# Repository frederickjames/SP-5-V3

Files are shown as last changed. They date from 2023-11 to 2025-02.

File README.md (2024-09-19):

# SP-5 V3

This project documents the work I've done in an attempt to make the Two Trees SP-5 V3 printer produce quality prints faster than the ol' reliable Ender 3 Pro. I hope some of this can help the community that, like me, purchases ~~cheap~~ less expensive stuff and enjoys the tinkering process.

### Summary of Project

- [Orange Pi Zero 3 for Klipper](/Orange%20Pi%20Zero%203/)
- [Klipper Config](/Klipper%20Config/)
- [Other modifications](/Other%20Modifications/)
 - [Hotend](/Other%20Modifications#v6-cheap-clone-hotend)
 - [ABL (3D Touch knockoff)](/Other%20Modifications#automatic-bed-leveling-and-probing)
 - [Silicone bed "springs"](/Other%20Modifications#springs)
 - [Z-Axis Changes](/Other%20Modifications#z-axis)

### Fixing Motion System

The linear rails were not smooth. On my priner the y-axis was particularly bad.  I finally got over my fear of losing all my bearings and broke down the linear rails to clean and lubricate.  I used Liquid Wrench to clean the rails and underside of the carriage then lubed with a little extra Super Lube applied by syringe.

To remove the carriage from the rails, invert the rail so the carriage is on the bottom the slowly slide it off the end of the rail trying to keep it as level as possible.  Once removed you'll see a row of ball bearings lightly held in place by a thin, flexible wire.  Take extra care when cleaning the underside of the carriage as any slight bump can cause the ball bearings to go flying (I wouldn't know anything about that).

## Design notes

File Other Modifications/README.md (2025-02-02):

# Other Modifications

Modifications were needed to tune this thing and make it print way nicer. Outside of updating to klipper and running it off of an Orange Pi, here are the modifications:

- All metal hotend (It's 2023, get the PTFE out of the melt zone)
- [Even better hotend solution](#v6-cheap-clone-hotend)
- [ABL (3D Touch knockoff)](#automatic-bed-leveling-and-probing)
- [Silicone bed "springs"](#springs)
- [Rigid shaft couplings between the stepper and the Z lead screws](#z-axis)
- [Oldham couplings for the Z lead screws](#z-axis)
- [Thrust Bearings to support the Z lead screws](#z-axis)

---

## All Metal Hotend

#### I have a [new solution](#v6-cheap-clone-hotend)

~~I found  some parts on Amazon that had close enough dimensions. I think they are a long way from good, but no worse than the stock setup.  I'll look around for hotend upgrades and update when I find something better.~~

- ~~[Some random Titanium Alloy Therman Heat Break](https://www.amazon.com/dp/B07JD2S4GK)~~
- ~~[Some cheap nozzles that are long enough to meet the heatbreak in the heater block](https://www.amazon.com/dp/B0C283TNWK)~~

~~You may also want to print [new 4010 Ducts](4010%20Duct%20Replacement.3mf). I only made these because I broke one of the existing ducts.  If you want to use it, you'll need to print it as is and a mirror for the left side.~~

---

## V6 (cheap clone) Hotend

I changed the hotend. The modifications I previously did where lackluster. I got tired of repairing and when it fell apart this time I just decided to replace.  I came across an old [YouTube from ModBot](https://www.youtube.com/watch?v=cXx1_OsDcIc) where he put an E3Dv6 on an older Two Trees coreXY.  Inspired by the mount he found, [I designed my own](V6%20Mount) and purchased a [cheap V6 clone from Amazon](https://www.amazon.com/dp/B0BR7Z63H8).

*UPDATE 2025-01-30: *I noticed that the bare plastic version where the M3 cut the threads was a little wobbly. It still printed, but I needed an excuse to make something. So I added a version with threaded inserts for the main body that holds the heatsink. You'll need 4 M3x6x5 threaded inserts.

---

## Automatic Bed Leveling and Probing

The knockoff kind of BL Touch that the Klipper documentation warns you about. It doesn't respond to the self test or some of the other diagnostic stuff, but it works.  You can see the setup in [the config file](../Klipper%20Config/printer.cfg).

Print [this crappy mount if you want](Touch%20Mount.3mf). ~~I may redesign later, but probably only if this one breaks or I take off the useless metal shroud it's attached to (more likely).~~

Offsets for crappy mount:  
x_offset: -33  
y_offset: 25  
z_offset: 3.00  

Or, when that one breaks becasue it's crap and you want to remove the useless metal shroud so you can see what's going on, you can [print this mount](Touch%20Mount%20-%20Back.3mf). It screws to the back of the print head where the rear shroud was attached. You will need longer M3 screws (I used M3x10mm, but 8mm would work too).

Offsets for less crappy mount:\
x_offset: 0\
y_offset: 25\
z_offset: 3.1

Both mounts are likely compatible with other Touch probes like the BL and Creality, but I have not tested.

- [3D Touch](https://www.amazon.com/dp/B09M9V8Y4Y "trust me, bro.")

---

## Springs

Probably not necessary, but I like them and they are cheap. I did have to make [some little spacers](SiliconeBedMountSpacers.3mf "put them on the bottom") to go under the Silicone springs becasue they were not tall enough.

- [3D Printer Heat Bed Leveling Parts](https://www.amazon.com/dp/B093Y89KS9)

---

## Z Axis

I was having a lot of trouble with z wobble and high pitch squeaking noise as the z axis moved so I looked at a bunch of videos and other stuff. Below is a list of what I did to change address the issue.
Starting from the bottom and working my way up, I put thrust bearings under the coupler to get the weaight of the Z assembly off the motors. They are held in place with a [little print](NEMA17_Thrust_Bearing_Holder.3mf) that fits over the heads of the motor mount screws.
Next up was replacing the flexible coupler. Using a flexible coupler to account for misaligned and wavy lead screws is low effort and does more to just allow the Z-axis to move than it does to correct the issue. I replaced with rigid shaft couplers. BUT only do this if you are addressing the lead screw binding with a different method (like oldham or wobblex).
Finally on the lead screw I added Oldham Couplers. Almost went with the WobbleX, but this thing called an Oldham showed up in search results and is like half the price so I gave it a try. I found [an adapter](https://www.printables.com/model/376711-sp-5-oldham-coupling-adapter) by [UNIT_normal](https://www.printables.com/@UNIT_normal_528315) on printables.

- [Thrust Bearings](https://www.amazon.com/gp/product/B07QLTXJDH "Maybe unneceary, but they are cheap.")
- [Rigid Shaft Coupling](https://www.amazon.com/dp/B08ZJ854Z6 "They don't do yoga")
- [Oldham](https://www.amazon.com/dp/B0BQMWC1VG "Named for leftovers past their prime.")

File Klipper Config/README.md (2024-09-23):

# Klipper Settings

### Printer Config
The [printer.cfg](printer.cfg) is based on the stock SP-5 V3 motherboard, Makerbase Robin Nano v3.1

### Macros
If you want to use the [macros](SP-5_V3_macro.cfg) for start/end, replace the existing start and end G-code with the following. The START_PRINT macro assumes you have a mesh named default. (Works in Cura, ymmv.)
#### Cura:
Start G-code:
```
START_PRINT BED_TEMP={material_bed_temperature_layer_0} EXTRUDER_TEMP={material_print_temperature_layer_0}
```
End G-code:
```
END_PRINT
```
#### Orca and similar:
Machine start G-code:
```
START_PRINT EXTRUDER_TEMP=[nozzle_temperature_initial_layer] BED_TEMP=[bed_temperature_initial_layer_single]
```
Machine end G-code:
```
END_PRINT
```

I moved my heatsync fan to J6 so it can be turned on/off as needed instead of always running. The printer.cfg file is set up for this, but it's optional to move the fan since J5 is always on. Do what you want, I'm not your dad. A word of warning, if you move the wrong plug then the case fans won't run all the time like they are currently set to so be sure you know which plug is case fans and which is hot end cooler.

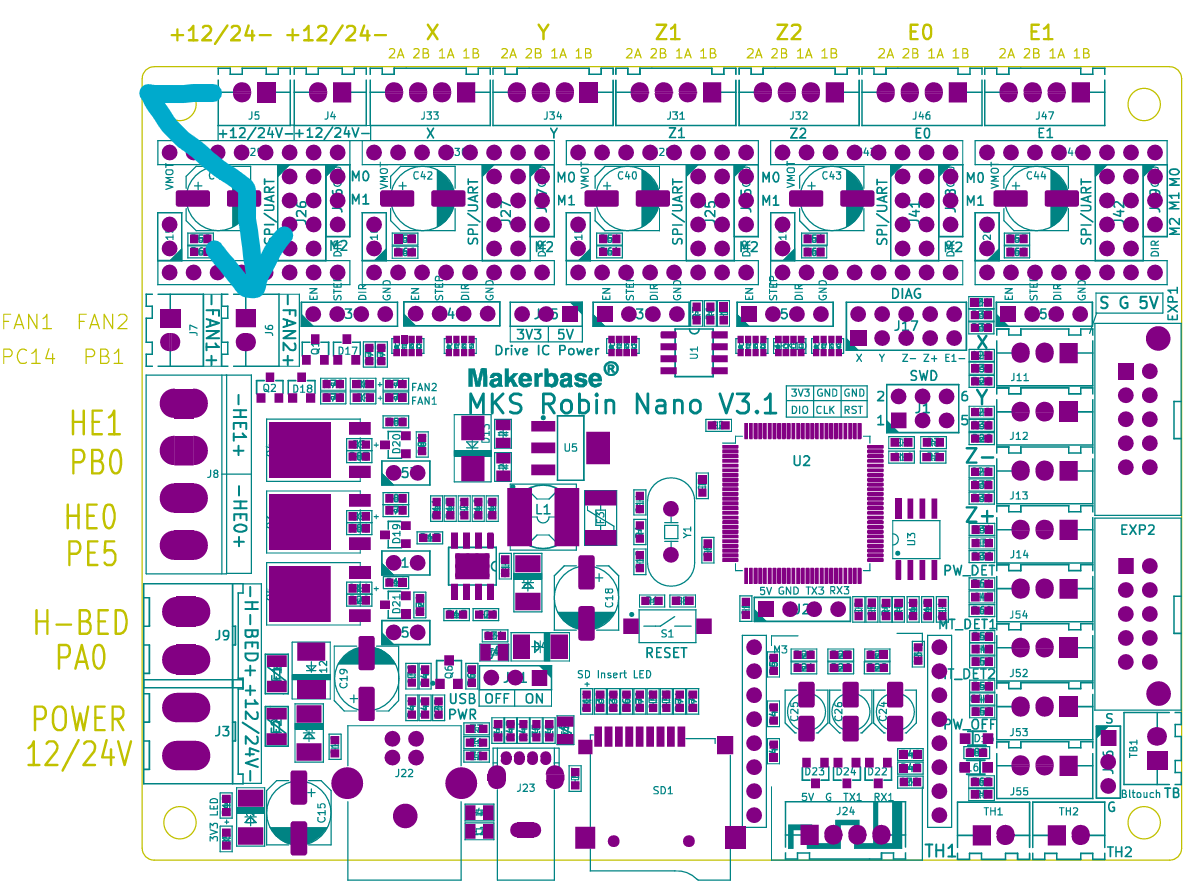
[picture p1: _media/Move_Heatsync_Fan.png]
J5 to J6 Optional Fan Move


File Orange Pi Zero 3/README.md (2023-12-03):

# Orange Pi Zero 3

This directory contains information on utilizing the Orange PI Zero 3 1.5G to run Klipper. Including the files to print a case for the board will replace the printers electronics cover. The case allows for access to the Orange PI's I/O through an enclsure built around the SP-5 V3 frame. You could probably just put whatever flavor of Pi you want under the deck with the rest of the electronics. Do what you want, I'm not youre dad.

I am using a UART connection between Orange Pi Zero 3 and the Robin Nano v3.1. UART setup on the Pi can be found [here on the Orange Pi Wiki](http://www.orangepi.org/orangepiwiki/index.php/Orange_Pi_Zero_3#26pin_UART_test). Pin connections depicted below, be sure to conenct Tx to Rx and Rx to Tx. Or just use USB if you want; I'm not your dad. But USB won't work with the case.

|Orange Pi Pin |Function | Function | Rodin Nano Pin|
|:---|:---|---:|---:|
|6|GND|GND|J2 Header - 2|
|8|TX|RX|J2 Header - 4|
|10|RX|TX|J2 Header - 3|

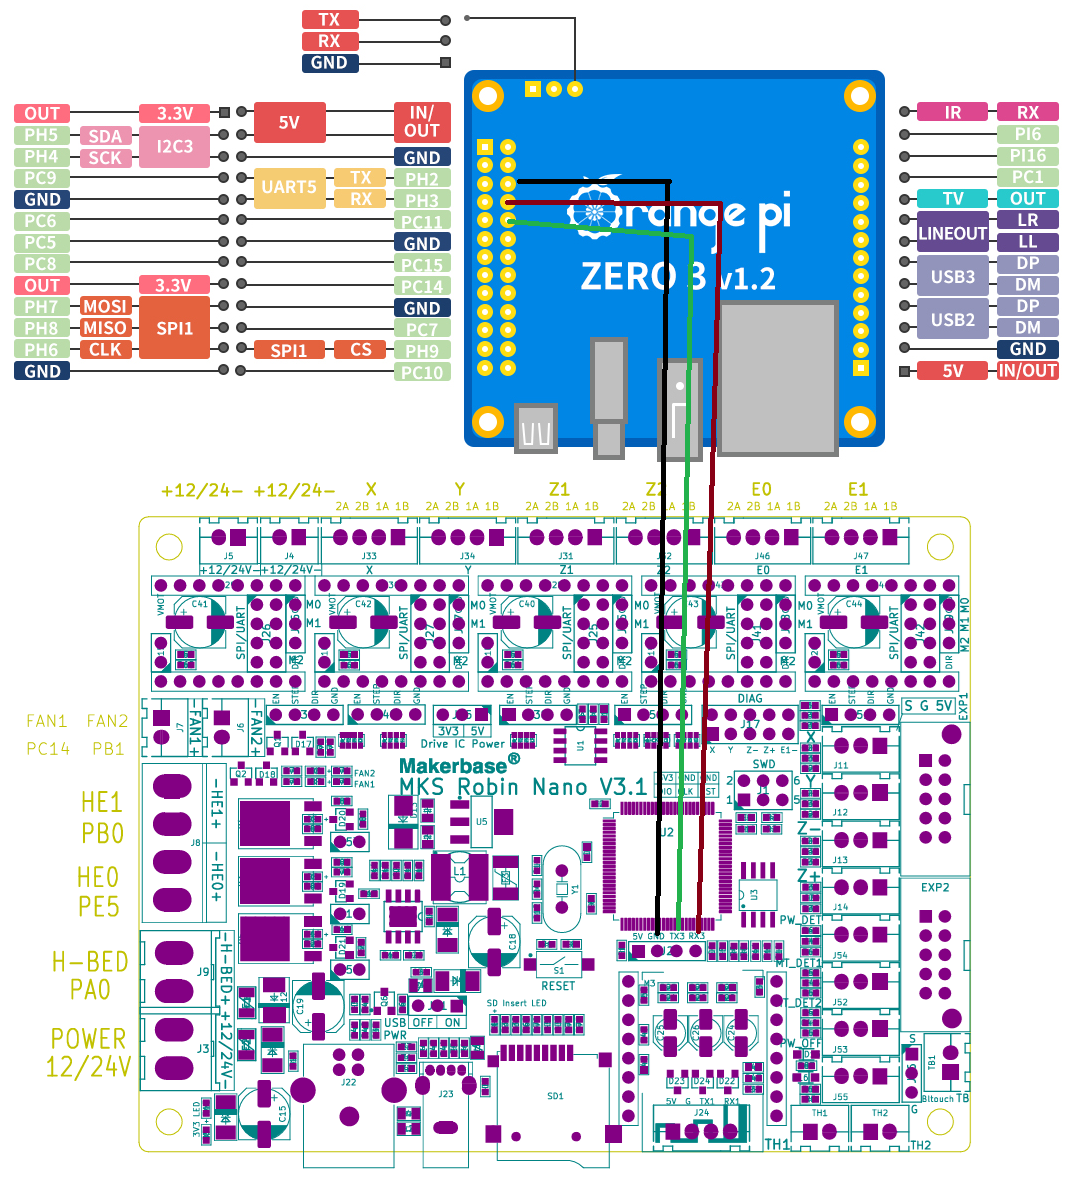
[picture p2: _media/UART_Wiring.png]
Cross the streams becasue you're not a ghost buster.


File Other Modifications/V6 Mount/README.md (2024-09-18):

# V6 (style) Hotend Bracket

I came across an old [YouTube from ModBot](https://www.youtube.com/watch?v=cXx1_OsDcIc) where he put an E3Dv6 on an older Two Trees coreXY.  Inspired by the mount he found, I designed one for the SP5-V3 and purchased a [cheap V6 clone from Amazon](https://www.amazon.com/dp/B0BR7Z63H8).  Inspired by the mount he found, [I designed my own](V6%20Hotend%20Mount.step).

It is basically a replacement for the bracke that the stock heatsink is attached too and reuses some stock parts.

There are 4 parts to print wth the Touch Mount being optional (if you don't use a touch probe, you don't need the mount). [Front](Front.3mf) and [Back](Back.3mf) are the pieces that hold the heatsink. They are held together by the fan mounting brackets that come with the printer and further supported when installed in the carriage. The [3010 mount](3010 mount.3mf) is screwed into the bottom of the Front. It reuses the 3010 fan from the heatsink that came with the printer. You'll need a new piece of PTFE tube since it's a bit further than before.

### To assemble:

1. Remove the stock hotend, heatsink fan, and 4010 blower fan mounts from the stock carriage and the extruder.
2. Attach the [3010 mount](3010%20mount.3mf) using 2 M3x10 screws from the top.
3. Clamp the [Front](Front.3mf) and [Back](Back.3mf) around the neck of the Heatsink and hold in place with the stock part cooler fan mounts using M3x6 (or M3x8). Right and left side are different - the nozzle should be lined up roughly with the middle of the fan mount.
4. Insert the new PTFE tube
    1. Cut a new piece of PTFE tubing. My final length is about 60.5 mm, but I would recommend you cut it a bit longer and trim it later.
    2. Place it into the hot end making sure it is firmly seated
    3. Slip the [PTFE Brace](PTFE%20Brace.3mf) over the tube with the notch at the top.  It's purpose is to keep the tube straight (I had some blowouts trying to push the filament too hard).
5. The assembly so far will attach to the carriage in the same location as the heatsink brack was removed reusing the M3x8 bolts, but it's a bit tricky.
    1. Slide the assembly up from the bottom passing the PTFE through the hole in the trolly. Make sure to align the notch at the top is facing the linear rail (the notch is allowance for the carriage)
    1. The 2 posts in the back of the assembly will go on the outside of the carriage. To insert the screw, I passed my Allen key through the front mounting holes then passed the M3 screw in from the side with tweezers so I could screw from inside.
    2. After the back is screwed in, you can insert the M3's to fasten the front.
6. Attach the stock part cooler fans and routh the cables as you see fit.
7. Optional: Add "heat shield" above nozzle.
    1. Measure the dimensions between the fan mounts and from front to back and determine (mine was 34mm wide x 37mm deep)
    2. Cut an aluminum can to these dimention plus a little bit wider.
    3. Use the extra width to bent the edges up in otder to give the shield a little more stiffness.
    4. Measure the depth of the heatsink and cut the aluminum to allow the shield to slide between the fins and around the core of the heatsink.
    5. Slide into place between the lowest 2 fins. It will keep the fan directed on the heatsink and away from the nozzle.
8. Install the heatsink fan. If you completed optional step 7, then the bottom of the fan should be in contact with the surface of the heat shield.
8. Replace the extruder assebmbly, trimming the PTFE tube to be the exact length needed.
9. Optional: Install touch probe.
    1. Fasten the probe to the mounting bracket from the bottom using M3x6 screws (or however yo want to fasten it).
    2. Loosly fasten the mount to the back of Back using M3x10 screws through the elongated holes and into the bottom set of holes on the main body.
    3. Adjust the mount to the desired height and tickets the screws to hold it in place.
10. PID tune the new hotend.
```
 PID_CALIBRATE HEATER=extruder TARGET=210
```

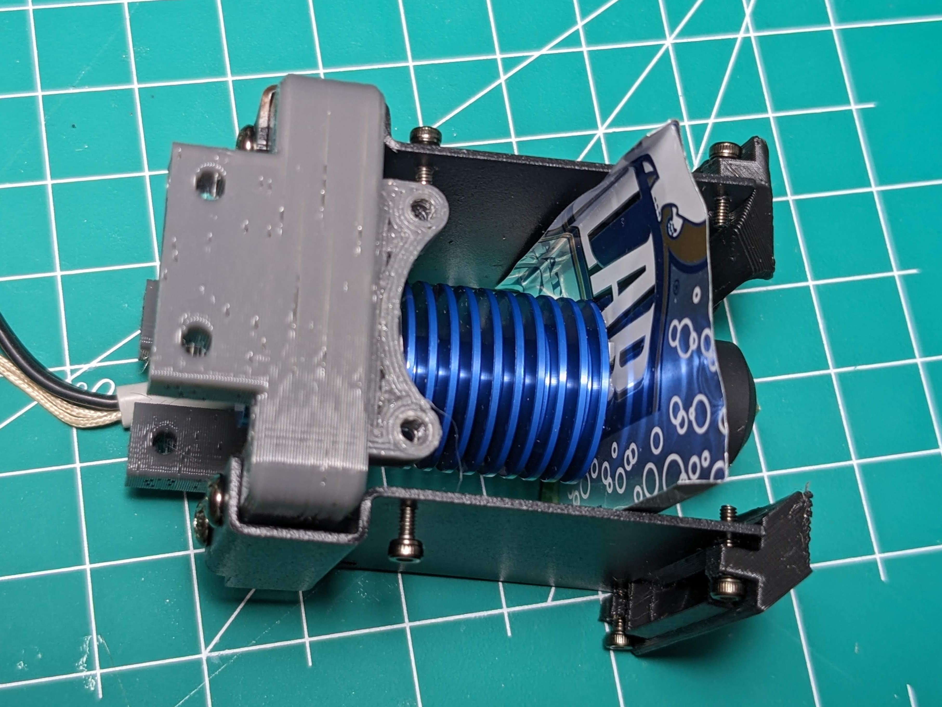
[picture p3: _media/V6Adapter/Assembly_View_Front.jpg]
Assembly front Assembly in progress, front view.

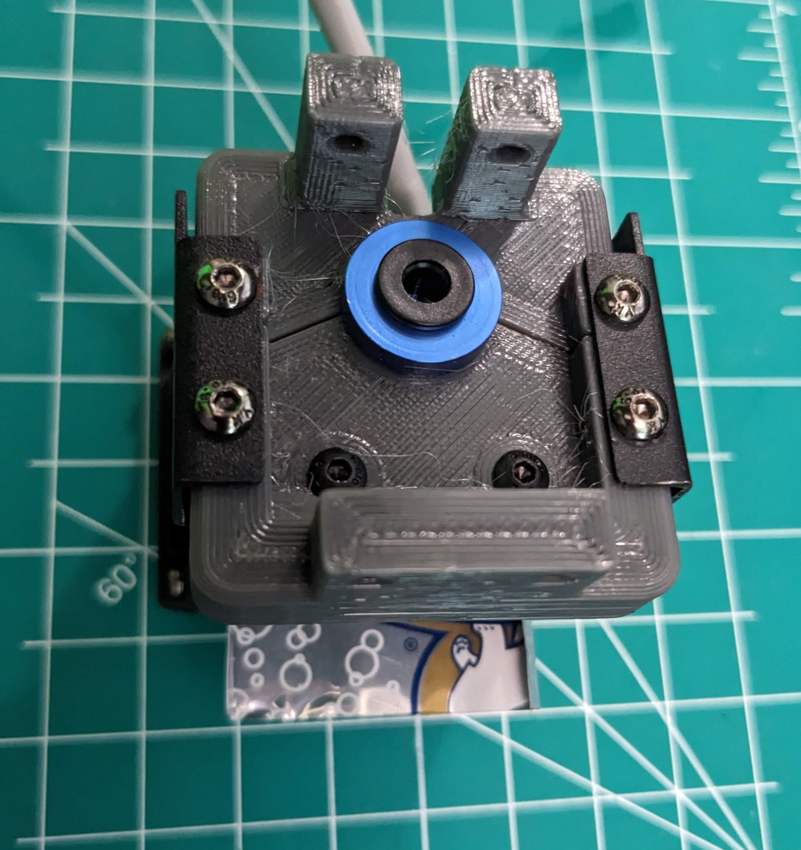
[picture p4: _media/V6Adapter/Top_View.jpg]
Assembly top Assembly in progress, top view.

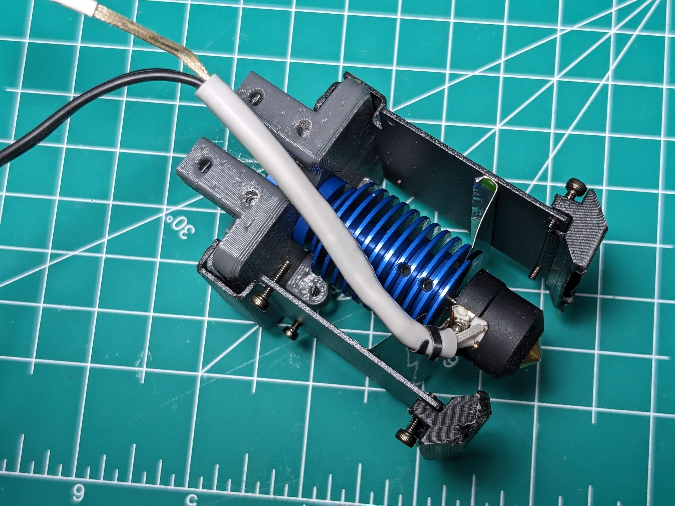
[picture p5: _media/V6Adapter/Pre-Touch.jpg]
Assembly back Assembly in progress, back view.

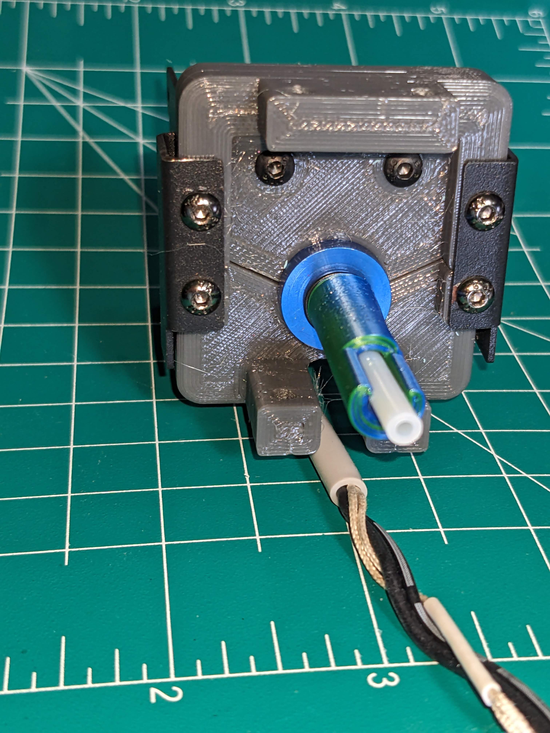
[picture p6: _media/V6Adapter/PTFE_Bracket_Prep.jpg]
PTFE Brace fitted It's pretty

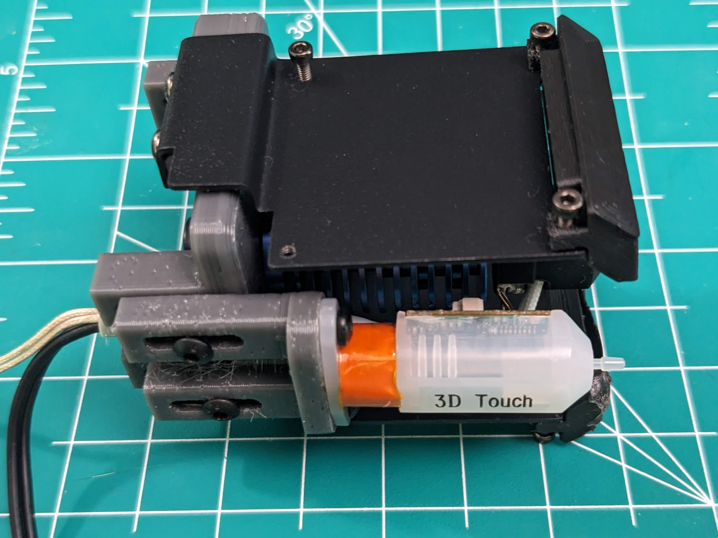
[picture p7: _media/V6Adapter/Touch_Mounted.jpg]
Assembly back quarter with touch mounted Assembly in progress, back quarter view.

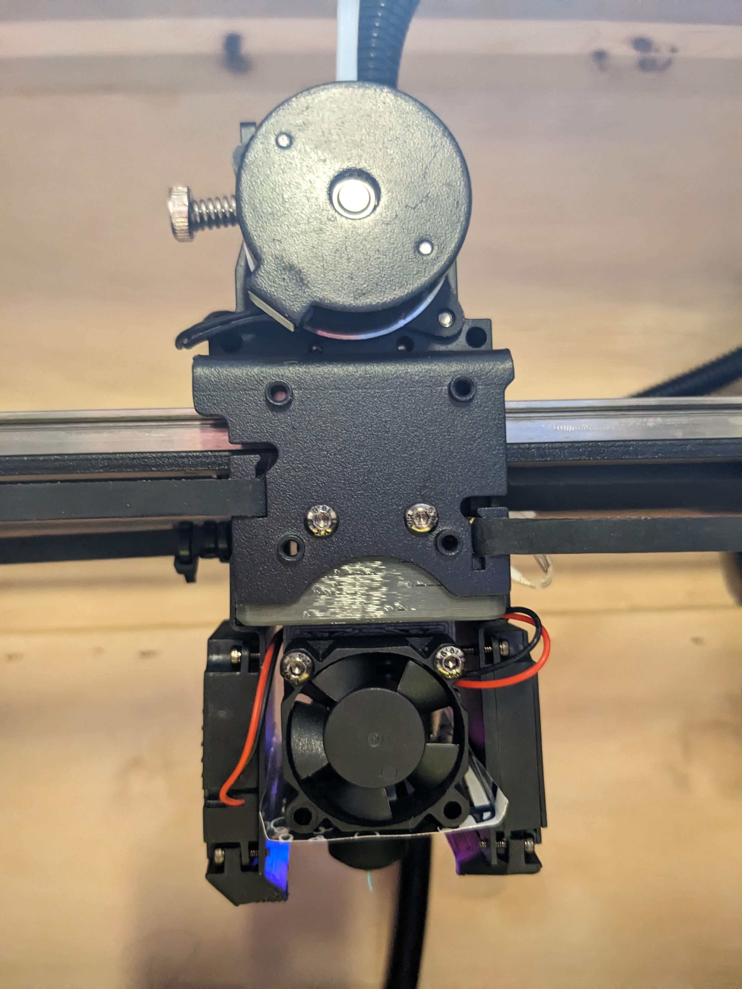
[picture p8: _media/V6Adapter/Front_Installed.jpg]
Front view.

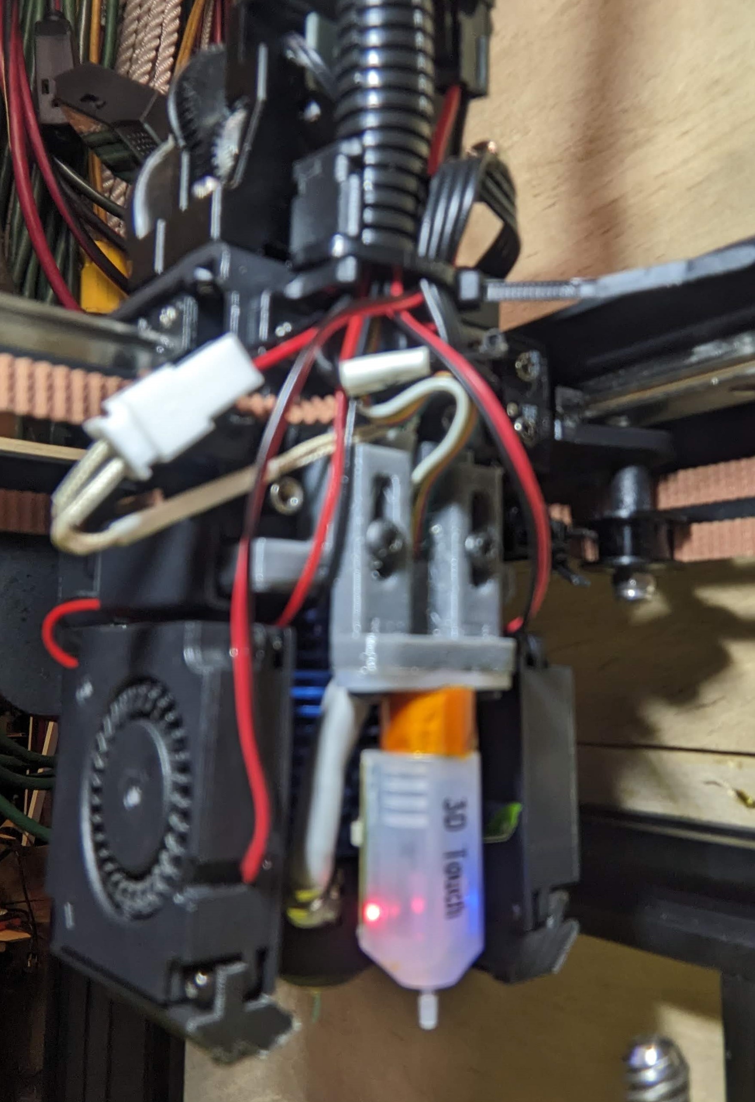
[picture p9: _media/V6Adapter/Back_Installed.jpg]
Out of focus back view.
.
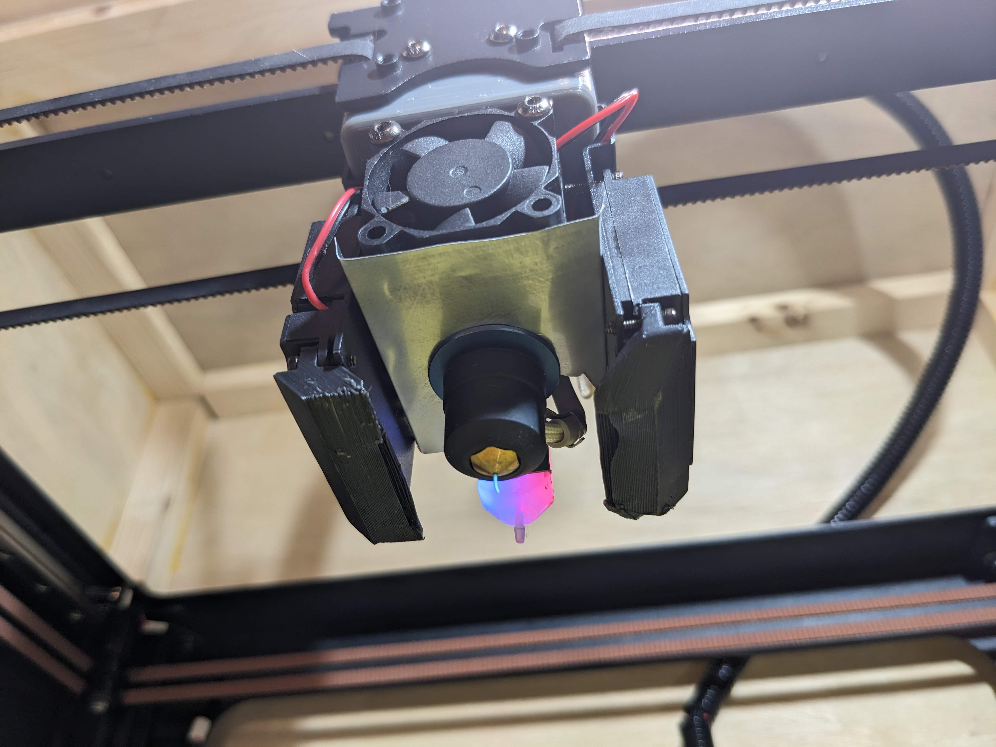
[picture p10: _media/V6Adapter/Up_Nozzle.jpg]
"Heat Shield" viewed from below Heat shield installed - bottom view.

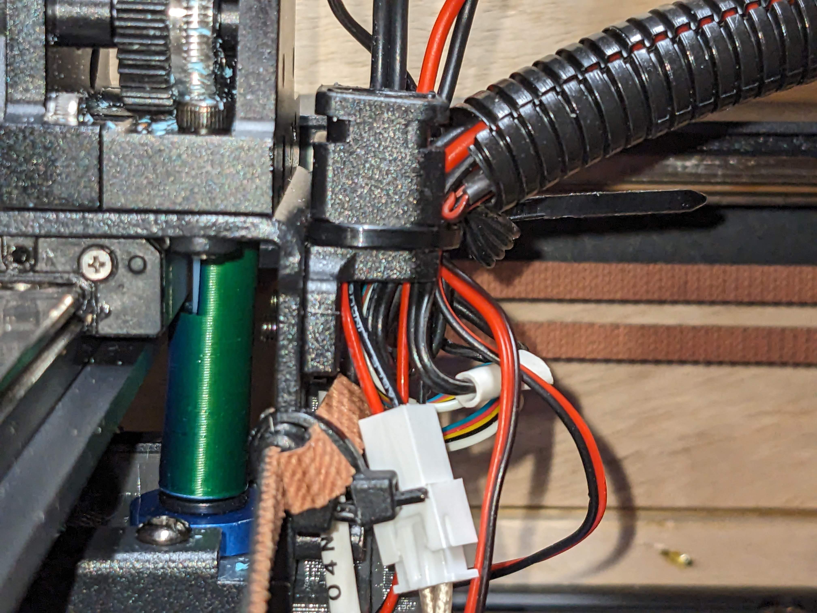
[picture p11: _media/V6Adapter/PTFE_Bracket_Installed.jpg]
PTFE Brce installed It's tight, but it fits.

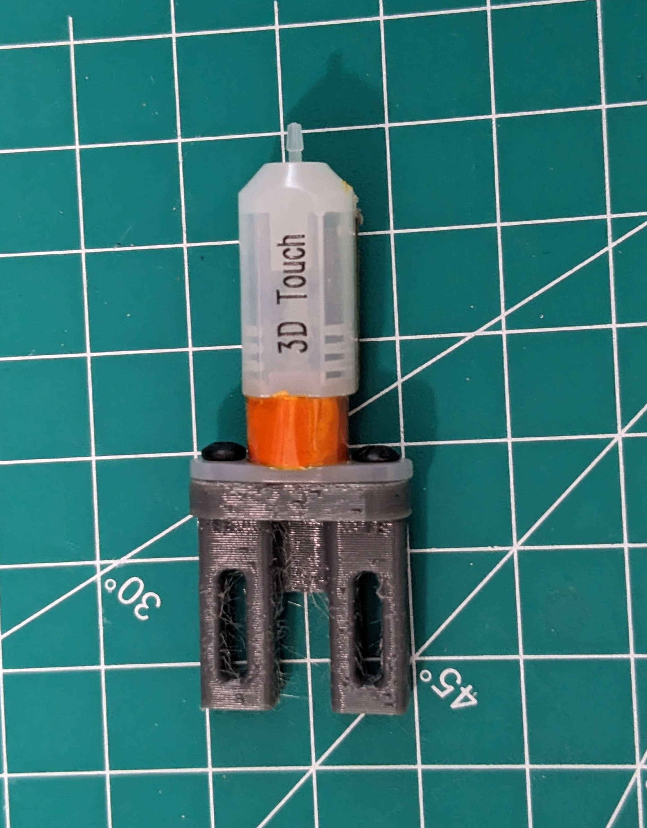
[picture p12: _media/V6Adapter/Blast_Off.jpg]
BLAST OFF!


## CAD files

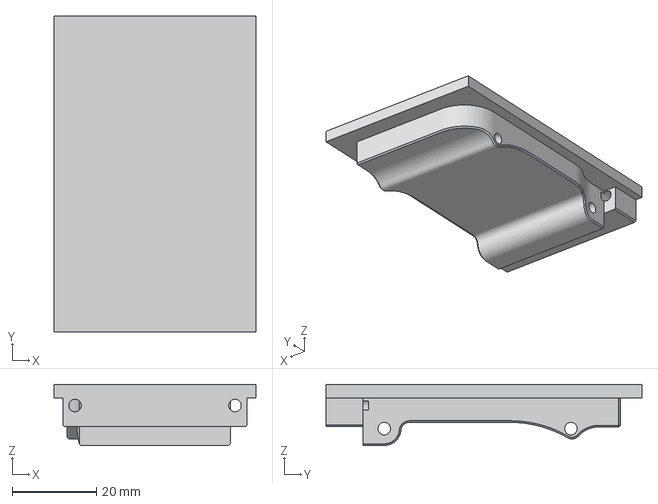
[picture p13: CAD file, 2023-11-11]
Orange Pi Zero 3/Top.3mf
48.0 x 75.0 x 14.5 mm

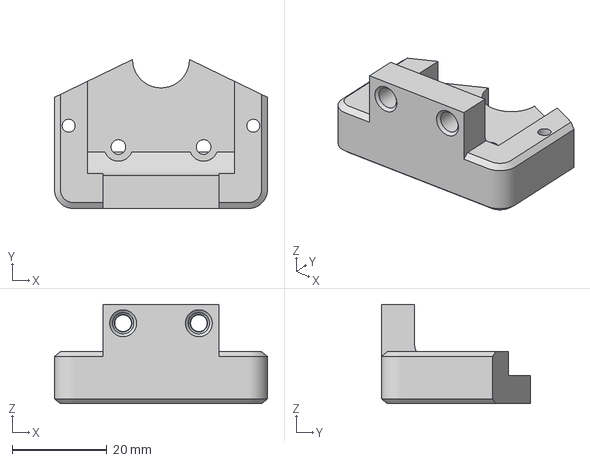
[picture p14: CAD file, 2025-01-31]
Other Modifications/Front.3mf
45.0 x 31.5 x 21.0 mm

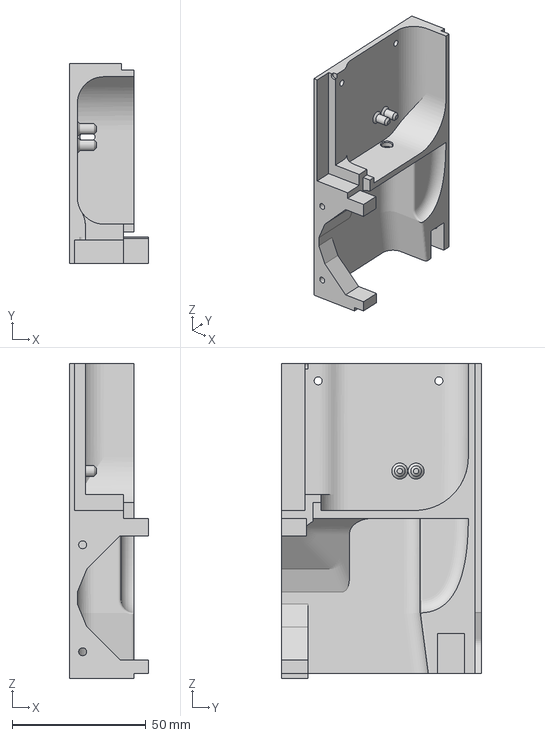
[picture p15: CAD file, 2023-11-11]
Orange Pi Zero 3/Side.3mf
29.7 x 75.0 x 117.9 mm

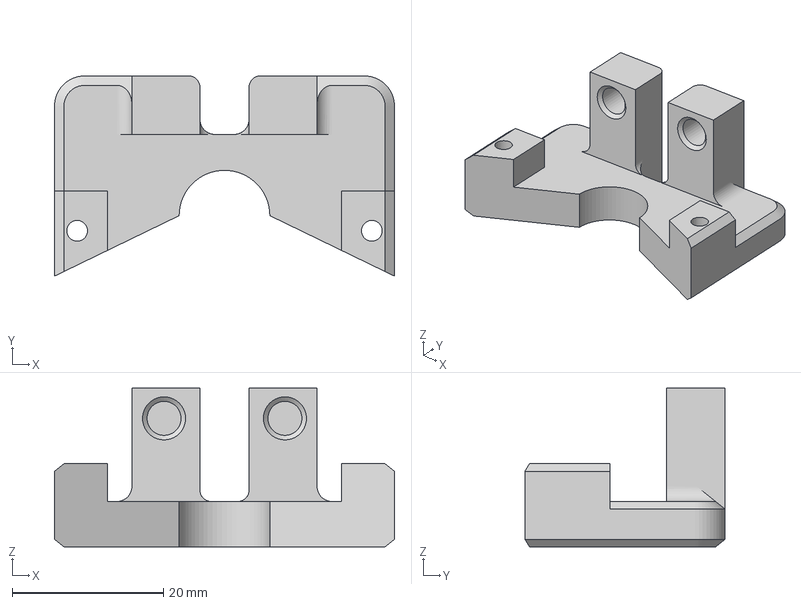
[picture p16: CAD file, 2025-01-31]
Other Modifications/Back.3mf
45.0 x 26.5 x 21.0 mm

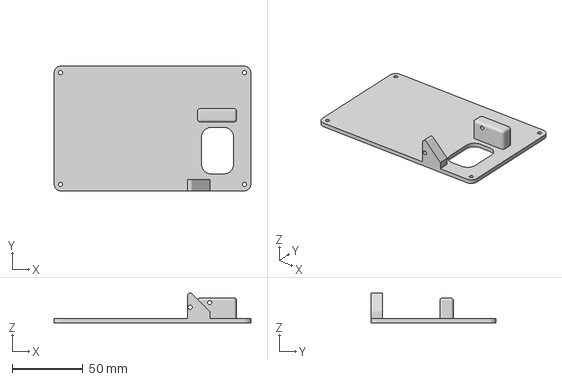
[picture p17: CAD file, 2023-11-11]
Orange Pi Zero 3/Cover Plate.3mf
139.3 x 88.3 x 21.2 mm

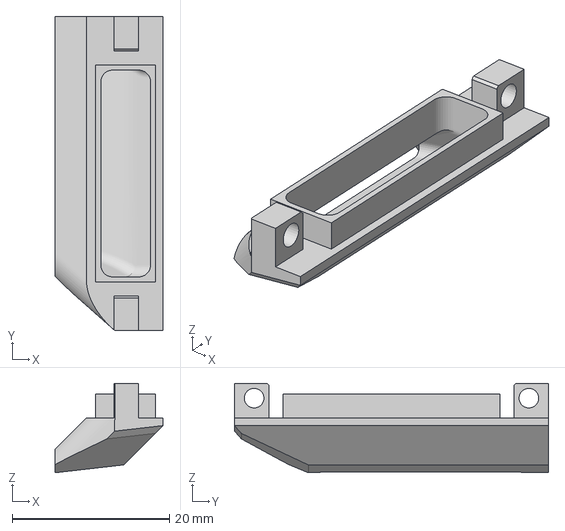
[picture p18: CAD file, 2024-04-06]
Other Modifications/4010 Duct Replacement.3mf
13.8 x 40.0 x 11.4 mm

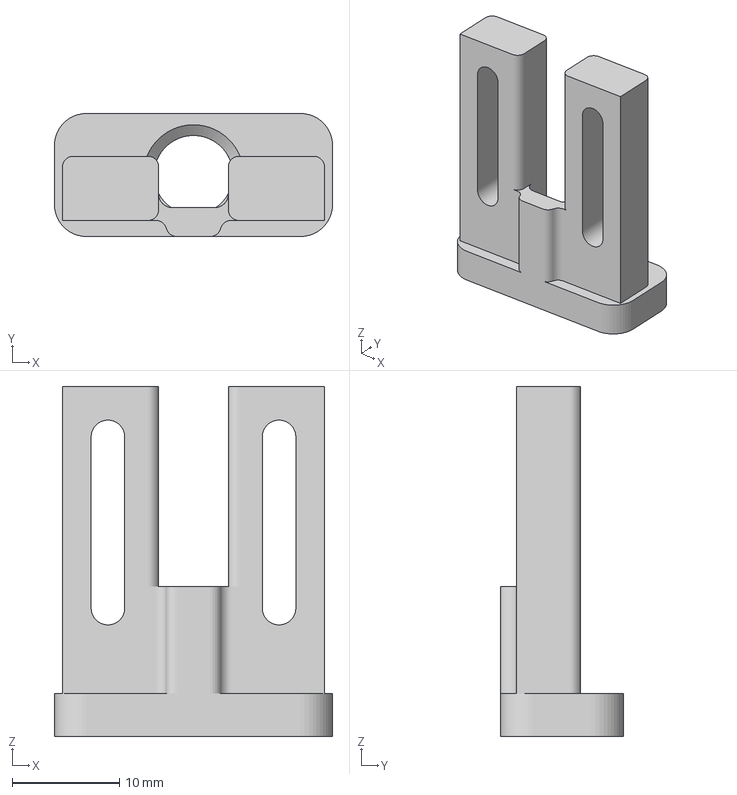
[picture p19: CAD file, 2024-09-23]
Other Modifications/V6 Mount/Touch Mount.3mf
26.0 x 11.5 x 32.7 mm

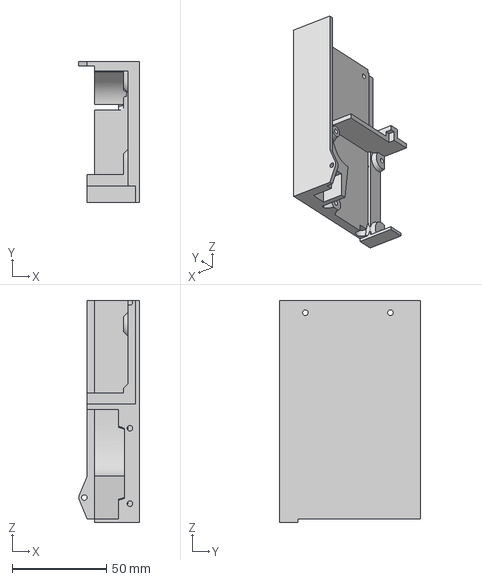
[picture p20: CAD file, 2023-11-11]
Orange Pi Zero 3/Holder.3mf
32.2 x 75.0 x 117.9 mm

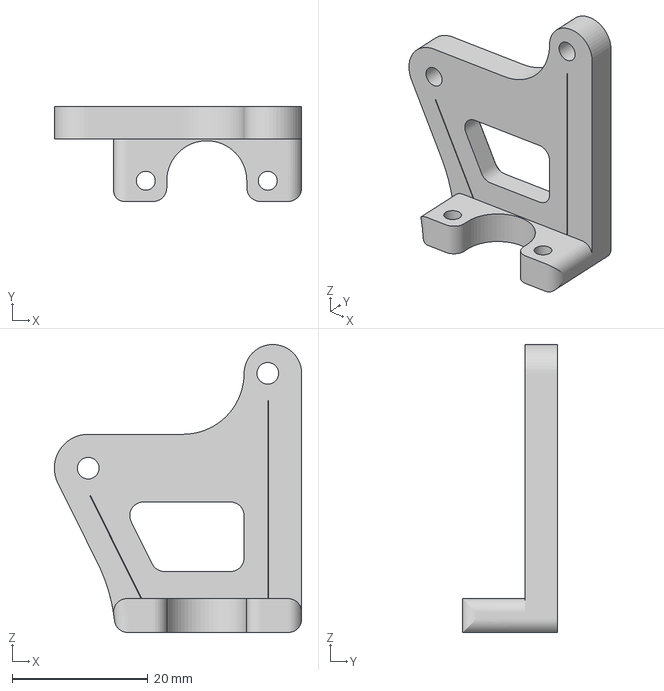
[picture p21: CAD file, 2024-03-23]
Other Modifications/Touch Mount - Back.3mf
36.5 x 14.0 x 42.5 mm

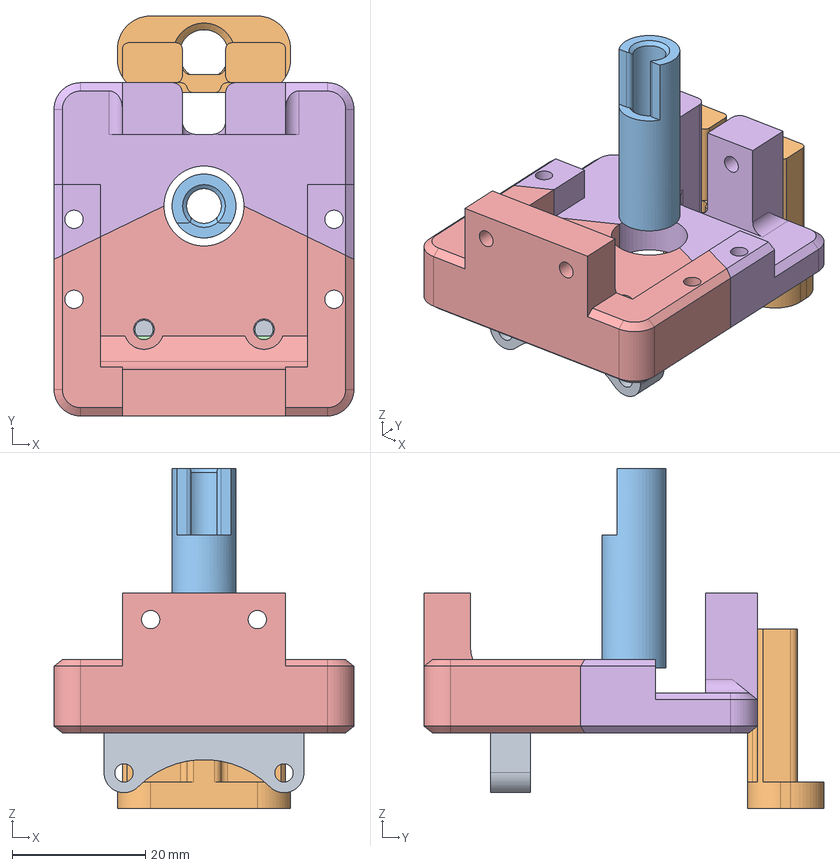
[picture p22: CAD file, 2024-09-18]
Other Modifications/V6 Mount/V6 Hotend Mount.step
45.0 x 60.0 x 51.1 mm
3010 Heasink Fan Mount
Touch Mount
PTFE Brace

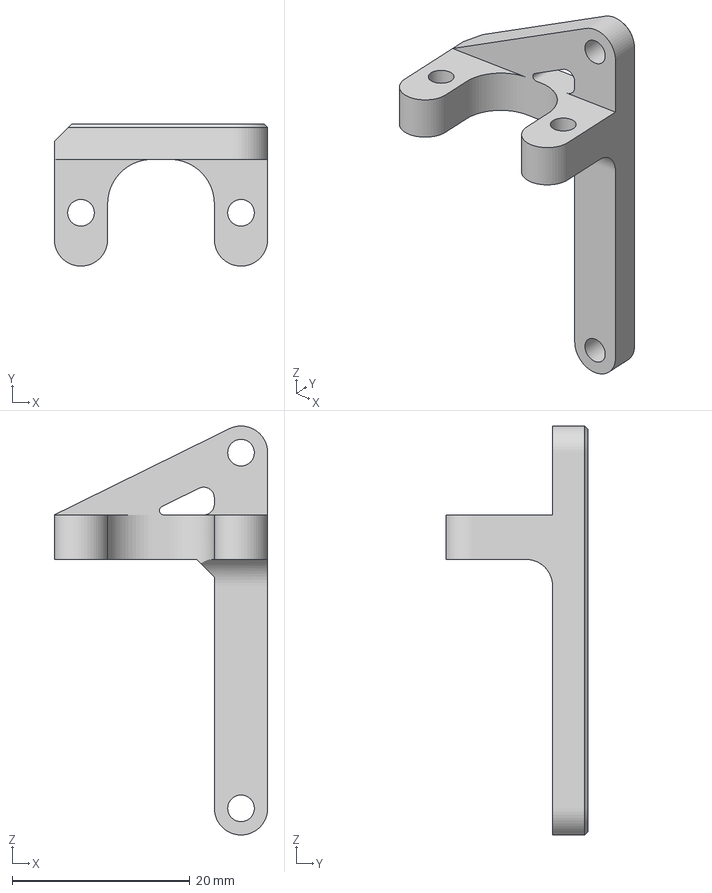
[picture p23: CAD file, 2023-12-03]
Other Modifications/Touch Mount.3mf
24.0 x 16.0 x 46.0 mm

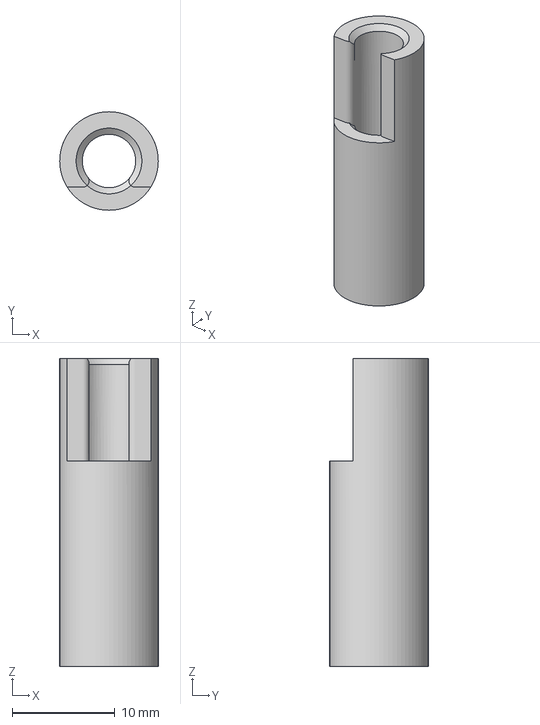
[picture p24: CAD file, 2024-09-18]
Other Modifications/V6 Mount/PTFE Brace.3mf
9.60 x 9.60 x 30.0 mm

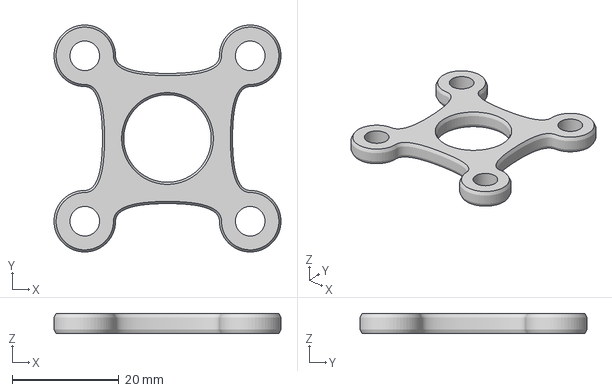
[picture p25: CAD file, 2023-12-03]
Other Modifications/NEMA17_Thrust_Bearing_Holder.3mf
42.5 x 42.5 x 3.80 mm

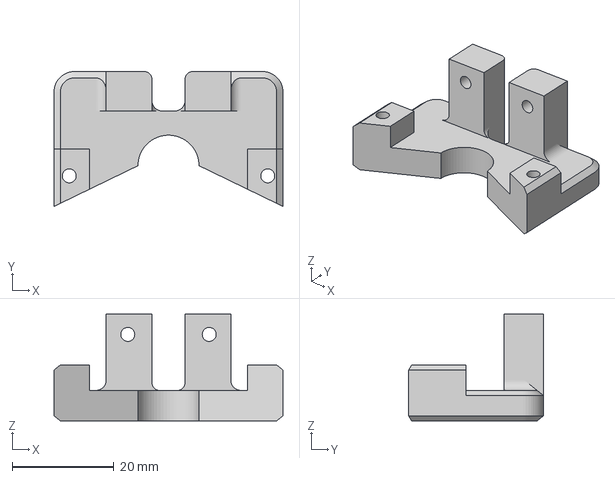
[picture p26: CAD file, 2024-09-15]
Other Modifications/V6 Mount/Back_selfThreaded.3mf
45.0 x 26.5 x 21.0 mm

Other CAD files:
Other Modifications/V6 Mount/Front_Inserts.3mf
Other Modifications/V6 Mount/Back_Inserts.3mf
Other Modifications/SiliconeBedMountSpacers.3mf
Other Modifications/V6 Mount/Front_selfThreaded.3mf
Other Modifications/V6 Mount/3010 mount.3mf

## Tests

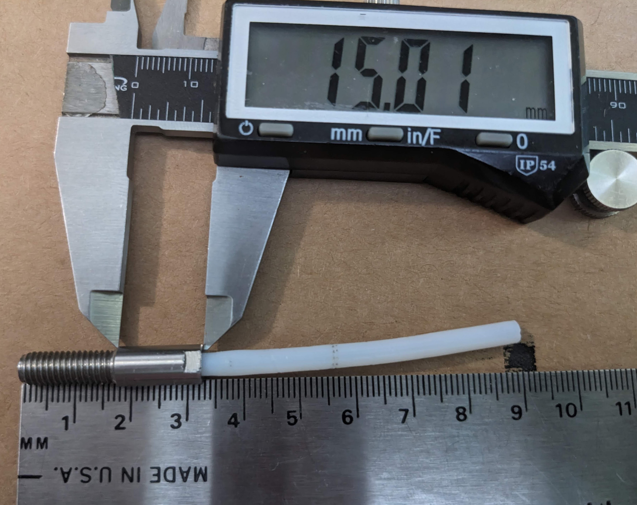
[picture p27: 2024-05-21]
_media/StockHeatbreakMeasurements.jpg

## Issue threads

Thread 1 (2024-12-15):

Belts

DrLabel, 2024-12-15:
What is the best way to tighten the Belts

frederickjames, 2024-12-16:
I've seen belt tensioners that you can print. Ans there are gauges and stuff that you can use to get them the same. But I just tried to match them by sound.

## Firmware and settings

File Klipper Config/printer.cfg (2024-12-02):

# This file contains common pin mappings for MKS Robin Nano V3
# boards. To use this config, the firmware should be compiled for the
# stm32f407. When running "make menuconfig", select the 48KiB
# bootloader, and enable "USB for communication".

# The "make flash" command does not work on the MKS Robin. Instead,
# after running "make", copy the generated "out/klipper.bin" file to a
# file named "Robin_nano_v3.bin" on an SD card and then restart the
# MKS Robin with that SD card.

# See docs/Config_Reference.md for a description of parameters.

[include mainsail.cfg]
[include SP-5_V3_macro.cfg]
[include Calibration_macro.cfg]
#[include adxl.cfg]

[stepper_x]
step_pin: PE3
dir_pin: !PE2
enable_pin: !PE4
microsteps: 16
rotation_distance: 40
endstop_pin: !PA15
position_min: 0
position_max: 300
position_endstop: 0
position_max: 300
homing_speed: 100

[tmc2209 stepper_x]
uart_pin: PD5
run_current: 1.2
hold_current: 0.6
#stealthchop_threshold: 99999

[stepper_y]
step_pin: PE0
dir_pin: !PB9
enable_pin: !PE1
microsteps: 16
rotation_distance: 40
endstop_pin: !PD2
position_endstop: 300
position_max: 300
position_min: 0
homing_speed: 100

[tmc2209 stepper_y]
uart_pin: PD7
run_current: 1.2
hold_current: 0.6
#stealthchop_threshold: 99999

[stepper_z]
step_pin: PB5
dir_pin: !PB4
enable_pin: !PB8
microsteps: 16
rotation_distance: 8
endstop_pin: probe:z_virtual_endstop
#endstop_pin: !PC8
#position_endstop: 0
position_min: -3
position_max: 320
homing_speed: 20

[tmc2209 stepper_z]
uart_pin: PD4
run_current: 1.2
hold_current: 0.6
#stealthchop_threshold: 99999

#[stepper_z1]
#step_pin: PA6
#dir_pin: !PA1
#enable_pin: !PA3
#microsteps: 32
#rotation_distance: 8

[extruder]
step_pin: PD6
dir_pin: !PD3
enable_pin: !PB3
microsteps: 16
gear_ratio: 9.5:1
rotation_distance: 53.4
nozzle_diameter: 0.400
filament_diameter: 1.750
max_extrude_only_distance: 200
heater_pin: PE5
sensor_type: Generic 3950
sensor_pin: PC1
min_temp: 0
max_temp: 260
control: pid
pid_Kp: 25.848
pid_Ki: 1.894
pid_Kd: 88.205
pressure_advance: 0.06

[tmc2209 extruder]
uart_pin: PD9
run_current: 1
hold_current: 0.500
#stealthchop_threshold: 99999

[firmware_retraction]
retract_length: 1.2
retract_speed: 50
unretract_extra_length: 0
unretract_speed: 30

[filament_switch_sensor RUNOUT]
switch_pin: !PA4
pause_on_runout: True
event_delay: 3.0
pause_delay: 0.5
#runout_gcode #gcode to be run at runout
#insert_gcode # what to do when refilled

[heater_bed]
heater_pin: PA0
sensor_type: EPCOS 100K B57560G104F # Stock
sensor_pin: PC0
min_temp: 0
max_temp: 100
control: pid
pid_Kp: 66.458
pid_Ki: 0.827
pid_Kd: 1335.806

[fan]
pin: PC14 # fan1
#pin: PB1 # fan2

[heater_fan hotend_fan]
pin: PB1
heater: extruder
heater_temp: 69.0

[mcu]
#serial: /dev/serial/by-id/usb-Klipper_stm32f407xx_000000000000000000000000-if00
serial: /dev/ttyS5
restart_method: command

[printer]
kinematics: corexy
max_velocity: 350
max_accel: 3000
max_z_velocity: 50
max_z_accel: 350
square_corner_velocity: 10.0

[exclude_object]

[bltouch]
sensor_pin: ^PC4
control_pin: PA8
x_offset: 0
y_offset: 22.8
z_offset: 1.30

[safe_z_home]
home_xy_position: 150,125
speed: 100
z_hop: 10
z_hop_speed: 5

[bed_mesh]
speed: 120
horizontal_move_z: 10
mesh_min: 5,23
mesh_max: 295,295
probe_count: 10,10
algorithm: bicubic
fade_start: .6
fade_end:2
fade_target:0
adaptive_margin: 0.5

[bed_screws]
screw1: 28,28
screw1_name: Lefty
screw2: 270,28
screw2_name: Righty
screw3: 272,272
screw3_name: Backy
screw4: 28,272
screw4_name: Backy Jr
horizontal_move_z: 10

[screws_tilt_adjust]
screw1:28,5.2
screw1_name: Lefty
screw2: 272,5.2
screw2_name: Righty
screw3: 272,249.2
screw3_name: Backy
screw4: 28,249.2
screw4_name: Backy Jr
screw_thread: CW-M4
horizontal_move_z: 10
speed: 200

[gcode_macro _CLIENT_VARIABLE]
variable_use_custom_pos   : True  ; use custom park coordinates for x,y [True/False]
variable_custom_park_x    : 295   ; custom x position; value must be within your defined min and max of X
variable_custom_park_y    : 5.0   ; custom y position; value must be within your defined min and max of Y
#variable_custom_park_dz   : 2.0   ; custom dz value; the value in mm to lift the nozzle when move to park position
#variable_retract          : 1.0   ; the value to retract while PAUSE
#variable_cancel_retract   : 5.0   ; the value to retract while CANCEL_PRINT
#variable_speed_retract    : 35.0  ; retract speed in mm/s
#variable_unretract        : 1.0   ; the value to unretract while RESUME
#variable_speed_unretract  : 35.0  ; unretract speed in mm/s
#variable_speed_hop        : 15.0  ; z move speed in mm/s
#variable_speed_move       : 100.0 ; move speed in mm/s
#variable_park_at_cancel   : False ; allow to move the toolhead to park while execute CANCEL_PRINT [True/False]
#variable_park_at_cancel_x : None  ; different park position during CANCEL_PRINT [None/Position as Float]; park_at_cancel must be True
#variable_park_at_cancel_y : None  ; different park position during CANCEL_PRINT [None/Position as Float]; park_at_cancel must be True
## !!! Caution [firmware_retraction] must be defined in the printer.cfg if you set use_fw_retract: True !!!
#variable_use_fw_retract   : False ; use fw_retraction instead of the manual version [True/False]
#variable_idle_timeout     : 0     ; time in sec until idle_timeout kicks in. Value 0 means that no value will be set or restored
#variable_runout_sensor    : ""    ; If a sensor is defined, it will be used to cancel the execution of RESUME in case no filament is detected.
##                                   Specify the config name of the runout sensor e.g "filament_switch_sensor runout". Hint use the same as in your printer.cfg
## !!! Custom macros, please use with care and review the section of the corresponding macro.
## These macros are for simple operations like setting a status LED. Please make sure your macro does not interfere with the basic macro functions.
## Only  single line commands are supported, please create a macro if you need more than one command.
#variable_user_pause_macro : ""    ; Everything inside the "" will be executed after the klipper base pause (PAUSE_BASE) function
#variable_user_resume_macro: ""    ; Everything inside the "" will be executed before the klipper base resume (RESUME_BASE) function
#variable_user_cancel_macro: ""    ; Everything inside the "" will be executed before the klipper base cancel (CANCEL_PRINT_BASE) function
gcode:

########################################
# EXP1 / EXP2 (display) pins
########################################

[board_pins]
aliases:
    # EXP1 header
    EXP1_1=PC5,  EXP1_3=PD13, EXP1_5=PE14, EXP1_7=PD11, EXP1_9=<GND>,
    EXP1_2=PE13, EXP1_4=PC6,  EXP1_6=PE15, EXP1_8=PD10, EXP1_10=<5V>,
    # EXP2 header
    EXP2_1=PA6, EXP2_3=PE8, EXP2_5=PE11, EXP2_7=PE12,  EXP2_9=<GND>,
    EXP2_2=PA5, EXP2_4=PE10, EXP2_6=PA7, EXP2_8=<RST>, EXP2_10=<3.3v>
    # Pins EXP2_1, EXP2_6, EXP2_2 are also MISO, MOSI, SCK of bus "ssp1"

#*# <---------------------- SAVE_CONFIG ---------------------->
#*# DO NOT EDIT THIS BLOCK OR BELOW. The contents are auto-generated.
#*#
#*# [bed_mesh default]
#*# version = 1
#*# points =
#*# 	0.315000, 0.270000, 0.237500, 0.197500, 0.200000, 0.180000, 0.195000, 0.217500, 0.255000, 0.325000
#*# 	0.325000, 0.292500, 0.252500, 0.237500, 0.165000, 0.202500, 0.200000, 0.205000, 0.260000, 0.265000
#*# 	0.302500, 0.270000, 0.215000, 0.192500, 0.152500, 0.165000, 0.185000, 0.247500, 0.272500, 0.257500
#*# 	0.300000, 0.267500, 0.237500, 0.185000, 0.157500, 0.187500, 0.175000, 0.230000, 0.262500, 0.270000
#*# 	0.302500, 0.232500, 0.220000, 0.162500, 0.130000, 0.142500, 0.210000, 0.222500, 0.270000, 0.262500
#*# 	0.290000, 0.220000, 0.187500, 0.190000, 0.122500, 0.157500, 0.187500, 0.210000, 0.240000, 0.272500
#*# 	0.280000, 0.272500, 0.232500, 0.172500, 0.160000, 0.210000, 0.217500, 0.262500, 0.272500, 0.297500
#*# 	0.345000, 0.307500, 0.250000, 0.225000, 0.255000, 0.240000, 0.260000, 0.270000, 0.292500, 0.300000
#*# 	0.317500, 0.287500, 0.240000, 0.262500, 0.230000, 0.235000, 0.260000, 0.267500, 0.295000, 0.282500
#*# 	0.347500, 0.290000, 0.235000, 0.230000, 0.177500, 0.195000, 0.217500, 0.237500, 0.255000, 0.270000
#*# x_count = 10
#*# y_count = 10
#*# mesh_x_pps = 2
#*# mesh_y_pps = 2
#*# algo = bicubic
#*# tension = 0.2
#*# min_x = 5.0
#*# max_x = 294.98
#*# min_y = 23.0
#*# max_y = 294.98
#*#
#*# [bltouch]
#*# z_offset = 1.285

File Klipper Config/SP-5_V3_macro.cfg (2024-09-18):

######################################################################
# Start Print and End Print
######################################################################

# Replace the slicer's custom start and end g-code scripts with
# START_PRINT and END_PRINT.

[gcode_macro START_PRINT]
gcode:
    {% set BED_TEMP = params.BED_TEMP|default(69)|float %}
    {% set EXTRUDER_TEMP = params.EXTRUDER_TEMP|default(169)|float %}
    #Set the units
    G21

    # Start bed heating
    M107
    M140 S40

    # Use absolute coordinates
    G90

    # Reset Extruder
    G92 E0

    # Reset the G-Code Z offset (adjust Z offset if needed)
    SET_GCODE_OFFSET Z=0.0

    # Wait for bed to reach temperature
    M190 S{BED_TEMP}

    # Home and Calibrate Adaptive Mesh
    G28
    BED_MESH_CALIBRATE ADAPTIVE=1

    # Set and wait for nozzle to reach temperature
    M109 S{EXTRUDER_TEMP} 

    #priming and junk
    G0 Z2.0 F600;
    G0 X295 Y100 F10000;
    G92 E0.0 ; reset extruder distance position；
    G0 Z0.5 F600;
    G1 Y200.0 E15 F3000.0 ; intro line
    G0 Z1.0 F600;
    G1 Y100.0 E15 F3000.0 ; intro line

    G0 X295 Y100 F12000;
    G1 Z0.5 F600;
    G0 X296 F6000;
    G1 Y101 F6000.0 ; intro line
    G0 X298 F12000;
    G1 Y201  F6000.0 ; intro line

    G0 Z2.0 F600;
    G92 E0.0 ; reset extruder distance position；

[gcode_macro END_PRINT]
gcode:
    # Chill Out
    M104 S0
    M140 S0

    # Relative positioning
    G91

    # Retract and raise Z
    G1 E-1 Z0.4 F2400

    # Wipe out
    G1 X-10 Y10 F3000

    # Raise Z more
    G1 Z2 F600
    G1 Z10

    # Absolute positioning
    G90

    #Move all the way out the way, please
    G1 X290 Y290 F6000 ;

    #Fan off
    M107

    #Stop your engines
    M84

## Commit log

2023-11-03 Gud 'nuff to sell configrashen
    [printer.cfg]
2023-11-03 300mm/s may have been false advertising
    [printer.cfg]
2023-11-06 3D Touch (the knockoff this heap deserves)
    [printer.cfg]
2023-11-06 Moved HE fan to a J6 header. and othe stuff
    [printer.cfg]
2023-11-06 Start/End Macro based on the Cura defaults & stuff
    [SP-5_V3_macro.cfg]
2023-11-06 adding macro and cfg cleanup
    [printer.cfg]
2023-11-09 tiny tweaks
    [printer.cfg]
2023-11-11 Re-org so much I'm like a corporation
    [Cover Plate.3mf, Holder.3mf, SP-5_V3_macro.cfg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]
2023-12-03 turn off stealthchop and some other adjustments
    [printer.cfg]
2023-12-03 adding some of the parts I designed
    [NEMA17_Thrust_Bearing_Holder.3mf, SiliconeBedMountSpacers.3mf, Touch Mount.3mf]
2023-12-04 Really important to get the folder names perfect and junk
    [NEMA17_Thrust_Bearing_Holder.3mf, SiliconeBedMountSpacers.3mf, Touch Mount.3mf]
2023-12-04 Updates to other modifications
    [NEMA17_Thrust_Bearing_Holder.3mf, SiliconeBedMountSpacers.3mf, Touch Mount.3mf]
2024-03-23 Bracket to hold 3D/BL Touch without shroud
    [Touch Mount - Back.3mf]
2024-03-23 Touch mount update
2024-03-26 updates, may be good, may be bad
    [printer.cfg]
2024-04-06 The duct on my fan broke when replacing the defective fan. This one works better for my nozzle
    [4010 Duct Replacement.3mf]
2024-05-21 Added image for reference to answer a questions about the stock heatsink.
2024-09-09 adding firmware retraction and some other tweaks
    [printer.cfg]
2024-09-09 surpeise, it's a typo
    [printer.cfg]
2024-09-15 New Volcane (clone) hotend, the mounts, and config changes
    [3010 mount.3mf, Back.3mf, Calibration_macro.cfg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]
2024-09-16 Have to include the step
    [Touch Mount.3mf, Volcano Hotend Mount.step]
2024-09-16 Who mesured the screw locations and offsets last time?
    [Calibration_macro.cfg]
2024-09-16 updates to the cfg stuff
    [SP-5_V3_macro.cfg, printer.cfg]
2024-09-16 minor changes for fun
    [printer.cfg]
2024-09-17 Changes for adaptive bed mesh.
    [SP-5_V3_macro.cfg, printer.cfg]
2024-09-18 changes and fixes
    [Calibration_macro.cfg, SP-5_V3_macro.cfg, printer.cfg]
2024-09-18 fixes and changes
    [printer.cfg]
2024-09-18 I broke it
    [Calibration_macro.cfg]
2024-09-18 Shore up the PTFE tube between the extruder and the heatsink
    [PTFE Brace.3mf]
2024-09-18 Making a mess
    [3010 mount.3mf, Back.3mf, Front.3mf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]
2024-09-18 Readme and additions for the PTFE Bracket
2024-09-18 PTFE Bracket details added to instructions
2024-09-18 PTFE Bracket instructions
2024-09-19 more mess
    [3010 mount.3mf, Back.3mf, Front and Back.3mf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]
2024-09-23 making it a little bit taller
    [Touch Mount.3mf]
2024-12-02 Update runout pin according to my configuration.
    [printer.cfg]
2024-12-02 fixed the macros and updated cgf changes
    [Calibration_macro.cfg, printer.cfg]
2024-12-02 always sync before you make changes
    [printer.cfg]
2025-01-31 Added version with threaded inserts
    [Back.3mf, Back_Insert.3mf, Back_selfThreaded.3mf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]
2025-01-31 updated docs and threaded insert hole size
    [Back_Insert.3mf, Back_Inserts.3mf, Front and Back.3mf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]
